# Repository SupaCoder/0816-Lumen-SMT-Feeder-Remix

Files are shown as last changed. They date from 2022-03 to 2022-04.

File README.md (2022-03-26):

# 0816 Lumen SMT Feeder Remix
 0816 SMT Automatic Feeder modified to work with the LumenPNP. Custom firmware written for an arduino nano with a servo sheild can run 12 feeders.

## Notes on printing and assembly
All the files need to be oriented to print correctly on your own printer.
use 0.2mm layer height for ALL parts

There is minimal post processing needed where bridging would help print things in thin air
no supports needed.

Assembly guide coming later when i have time.

Some things that i used
M3 screws for the big holes
M2.5 for the switch and servo armature and the tensioner on the lip
3D printer spring for the tape push down lever
elastic band for the spooler lever
M4 sized hole for mounting to the extrusion

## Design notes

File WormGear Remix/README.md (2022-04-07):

# WormGear Tape puller remix
 0816 SMT Automatic Feeder tape puller modified to better fit onto the feeder. Removed as many screws/pins as I could. 
## Notes on printing and assembly
All the files need to be oriented to print correctly on your own printer.
use 0.2mm layer height for ALL parts
Use Supports for the lever

use 0.1mm layer height for the failure gear with No supports. The outer shell is made to break away "easily" some cleanup required.

for installing the puller on the feeder put the top most screw in first then slide the tape puller onto that screw and put in the bottom one. after tightening both install the bottom motor last.

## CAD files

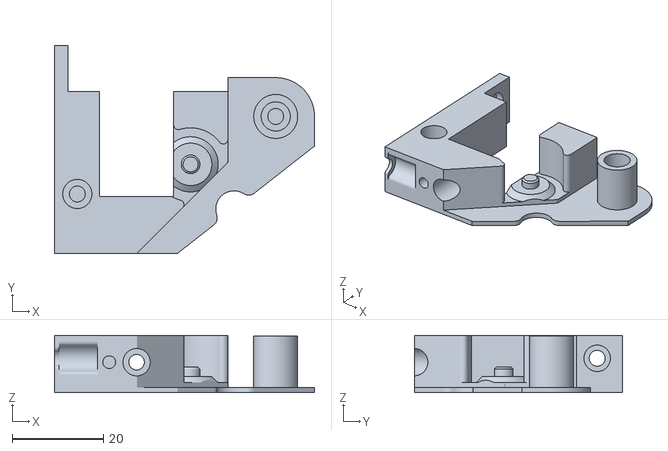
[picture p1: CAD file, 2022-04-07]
WormGear Remix/BodyMain.stl
57.0 x 45.5 x 12.6

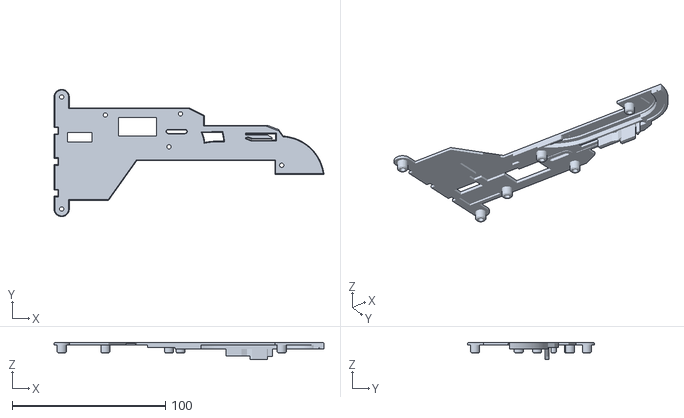
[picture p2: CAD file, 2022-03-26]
3D print files/base_cover.stl
176.1 x 83.0 x 11.2

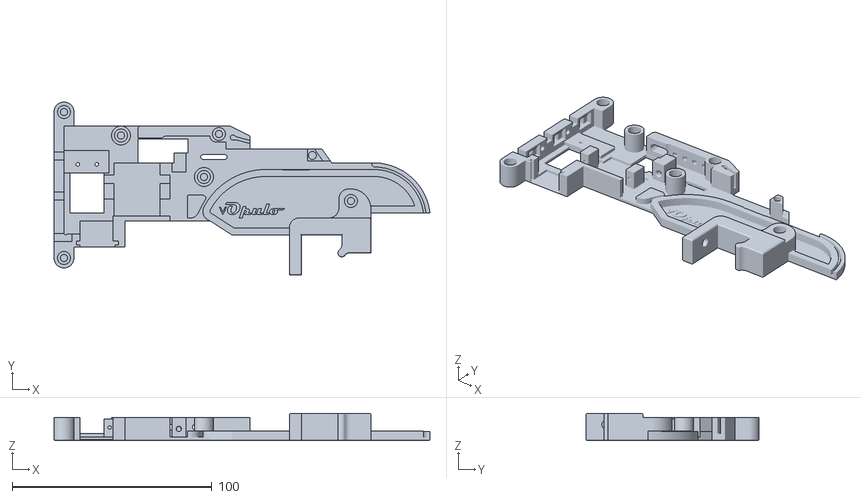
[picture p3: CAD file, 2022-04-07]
Longer Body Feeder/base.stl
188.1 x 86.5 x 13.7

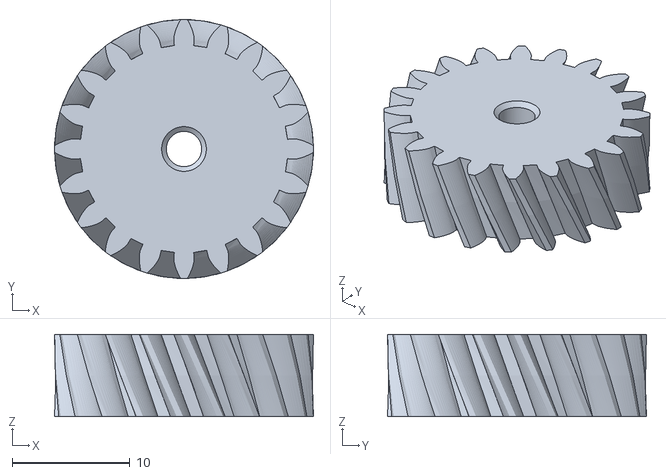
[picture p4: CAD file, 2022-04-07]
WormGear Remix/BigGear.stl
22.0 x 22.0 x 7.00

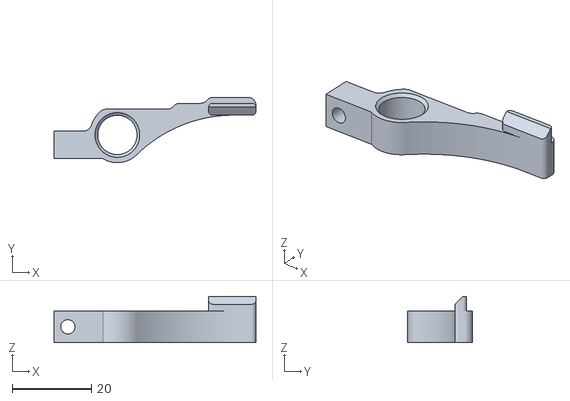
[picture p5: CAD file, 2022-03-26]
3D print files/tape_pushdown_springloaded.stl
51.0 x 16.5 x 11.7

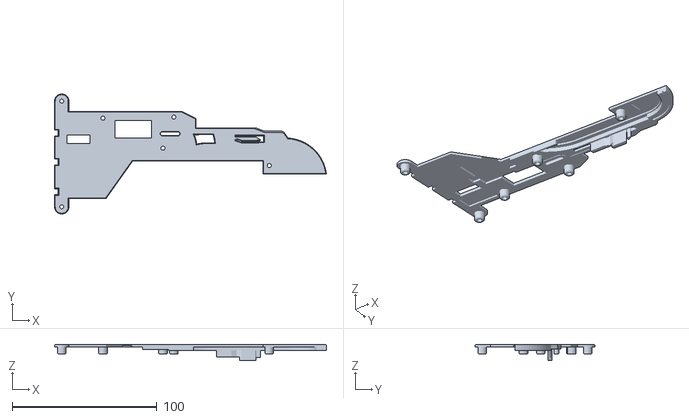
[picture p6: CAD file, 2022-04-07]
Longer Body Feeder/base_cover.stl
188.1 x 83.0 x 11.2

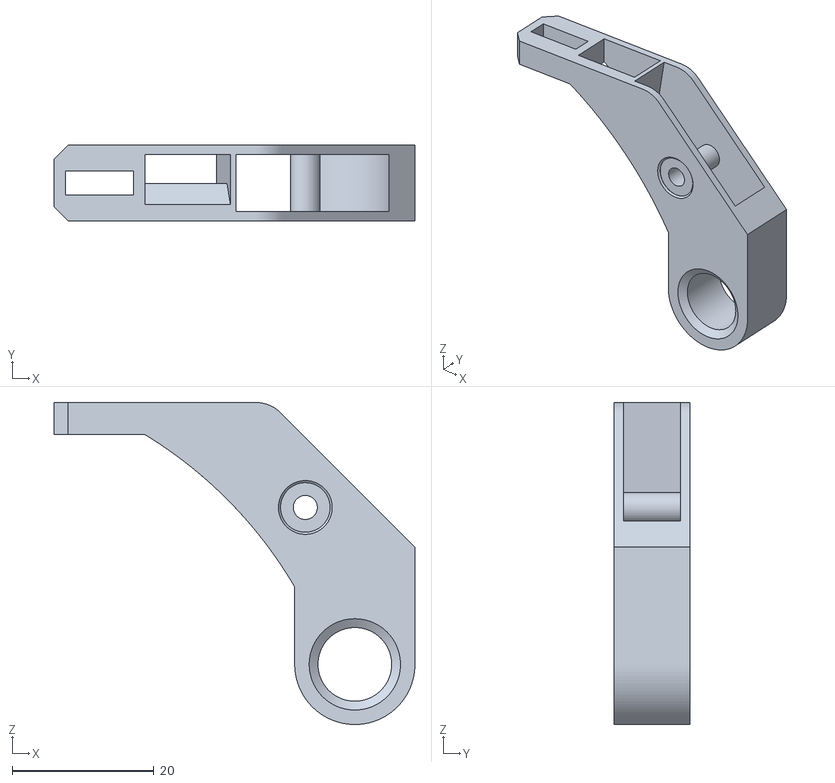
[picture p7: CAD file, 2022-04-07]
WormGear Remix/Lever.stl
51.0 x 10.8 x 45.5

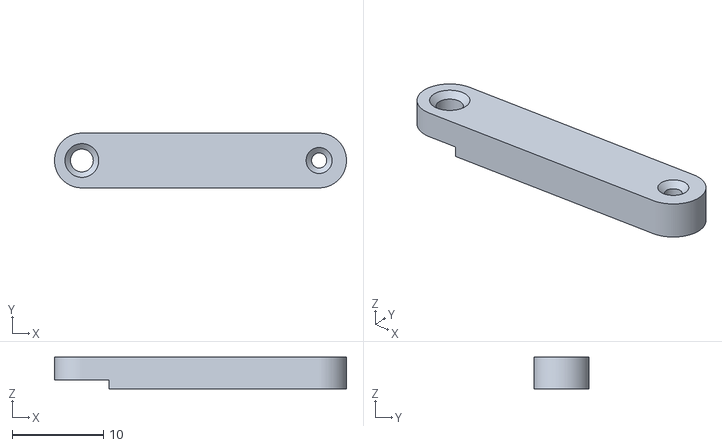
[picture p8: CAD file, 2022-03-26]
3D print files/lever_servo_advancer.stl
32.0 x 6.00 x 3.50

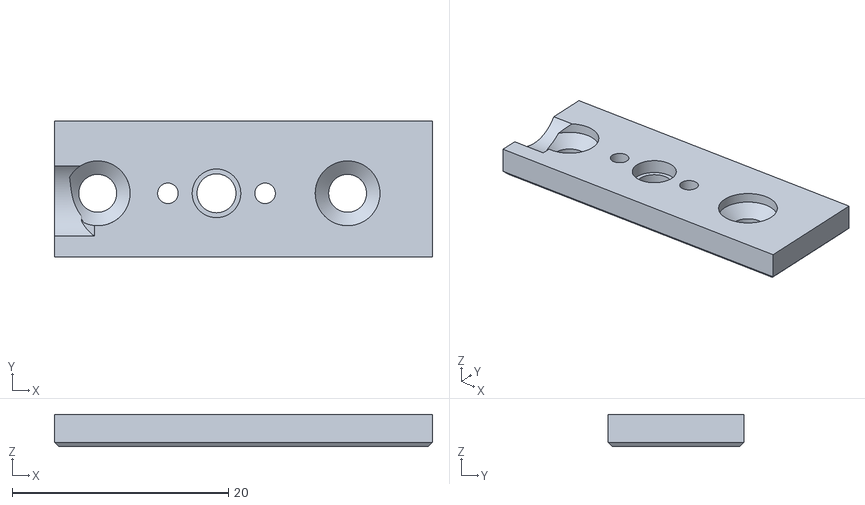
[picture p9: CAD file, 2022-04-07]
WormGear Remix/BodyMount.stl
35.0 x 12.6 x 3.00

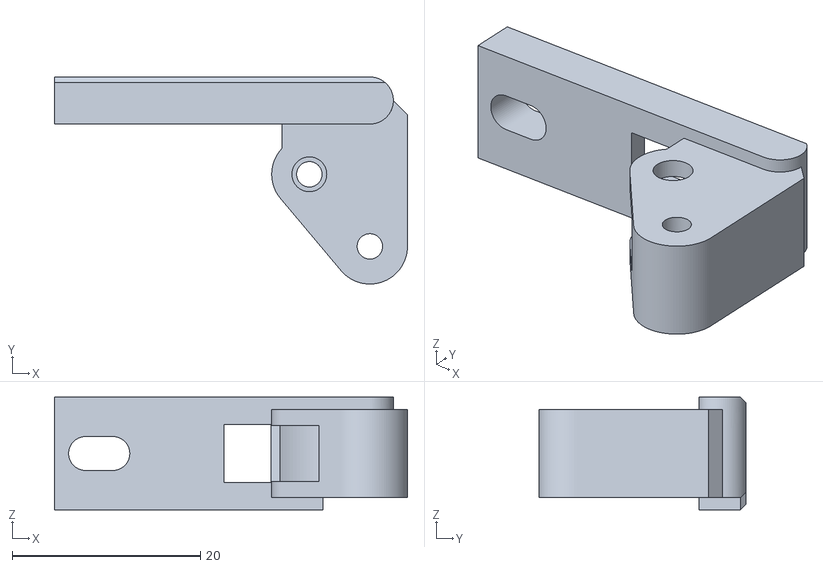
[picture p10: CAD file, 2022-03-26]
3D print files/vorspanner_rad.stl
37.5 x 22.0 x 12.0

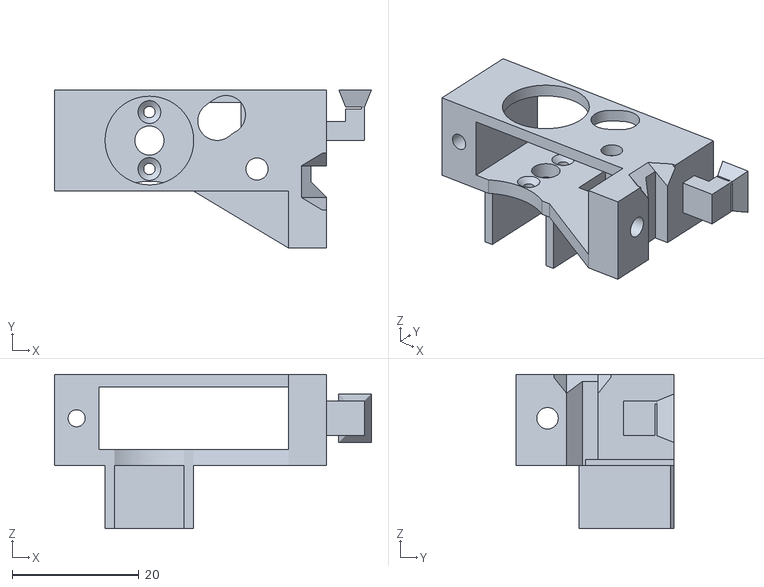
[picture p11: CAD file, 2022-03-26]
3D print files/spooler_mountplate_v2.stl
50.1 x 25.0 x 24.4

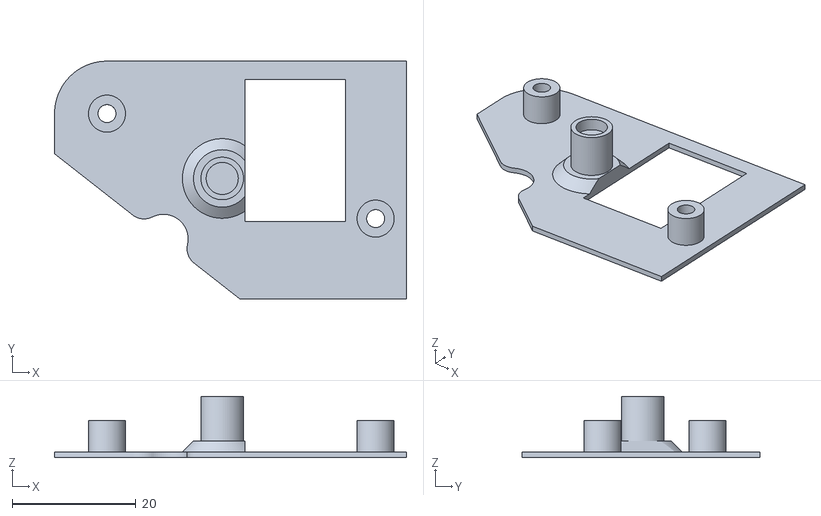
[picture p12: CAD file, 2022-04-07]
WormGear Remix/BodyCover.stl
57.0 x 38.5 x 9.90

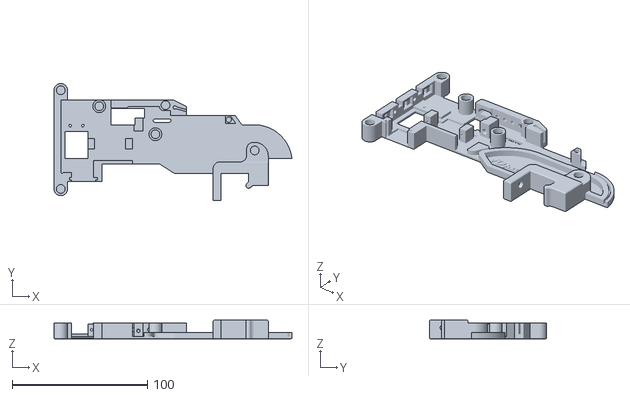
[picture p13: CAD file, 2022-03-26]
3D print files/base.stl
176.1 x 86.5 x 13.7

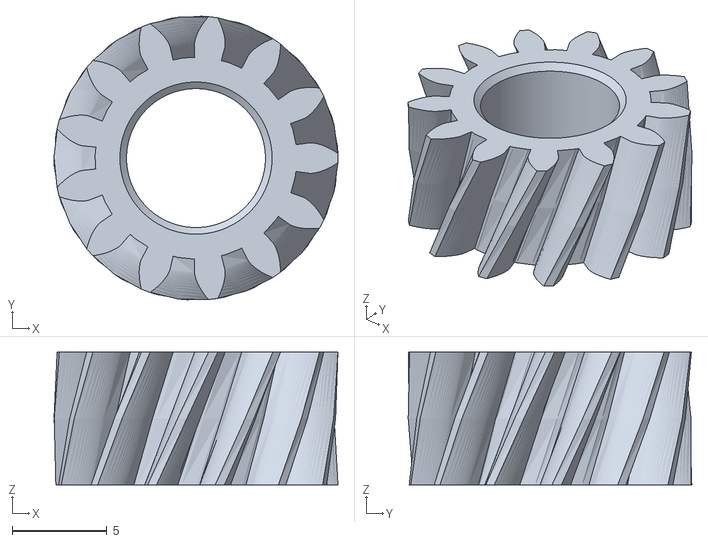
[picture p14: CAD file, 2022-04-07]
WormGear Remix/SmolGear.stl
15.0 x 15.0 x 7.00

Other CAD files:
3D print files/lever_coverswitch_pullingSpring.stl
3D print files/petg_spring_advancer.stl
3D print files/feeder_pin_new.stl
3D print files/DIN - Spur gear 0.7M 17T 20PA Spur gear.stl
3D print files/DIN - Spur gear.stl

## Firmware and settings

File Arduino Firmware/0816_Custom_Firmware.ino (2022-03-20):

#include <Servo.h>

Servo feeder0;
Servo feeder1;
Servo feeder2;
Servo feeder3;
Servo feeder4;
Servo feeder5;
Servo feeder6;
Servo feeder7;
Servo feeder8;
Servo feeder9;
Servo feeder10;
Servo feeder11;

String inData;
void setup() {

  Serial.begin(115200);
  Serial.println("Feeduino");
  Serial.println("ok");

  feeder0.attach(2);
  feeder1.attach(3);
  feeder2.attach(4);
  feeder3.attach(5);
  feeder4.attach(6);
  feeder5.attach(7);
  feeder6.attach(8);
  feeder7.attach(9);
  feeder8.attach(10);
  feeder9.attach(11);
  feeder10.attach(12);
  feeder11.attach(13);
  
//setFeeder(0, 129);
//setFeeder(0, 90);
}

//Fx a
//F - Feeder
//x - number
//a - value

//Fx S
//Feeder 1 Serve

//Set Fx R<> P<>
//Set Feeder x Retract and Push

void loop() {
  while (Serial.available() > 0) {
    char recieved = Serial.read();
    inData += recieved;

    if (recieved == '\n') {
      processCommand(inData);
      inData = "";
    }
  }
}

void processCommand(String inData) {
  inData.trim();
  inData.toUpperCase();
  Serial.print("ok");
  if(inData.startsWith("F")){
    String temp = inData.substring(1);
    servePart(temp.toInt());
    Serial.print(": Served F");
    Serial.print(temp.toInt());
    
  }
  
  Serial.println("");
}

void servePart(int feeder) {
  setFeeder(feeder, 80);//88
  delay(200);
  setFeeder(feeder, 140);
  delay(200);
  setFeeder(feeder, 129);
}

void setFeeder(int feeder, int value) {
  switch (feeder) {
    case 0:
      feeder0.write(value);
      break;
    case 1:
      feeder1.write(value);
      break;
    case 2:
      feeder2.write(value);
      break;
    case 3:
      feeder3.write(value);
      break;
    case 4:
      feeder4.write(value);
      break;
    case 5:
      feeder5.write(value);
      break;
    case 6:
      feeder6.write(value);
      break;
    case 7:
      feeder7.write(value);
      break;
    case 8:
      feeder8.write(value);
      break;
    case 9:
      feeder9.write(value);
      break;
    case 10:
      feeder10.write(value);
      break;
    case 11:
      feeder11.write(value);
      break;
    default:
      break;
  }
}

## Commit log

2022-03-20 Initial commit
    Early working version of the feeder. consider this a Beta, as it will be modified as time goes on and tuned to be a better design
    [DIN - Spur gear 0.7M 17T 20PA Spur gear.stl, DIN - Spur gear.stl, PCB Bracket v1.stl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]
2022-03-26 Many Tweeks to the 3D files.
    Fixed issue with servo missfitment
    Added port for switch pins
    Lever now has external feature to aid in loading and unloading tape
    clearence on the exit improved for larger components
    added a tensioner for the cover that prevents the components from flying out
    Extended stroke of the advancer to aid in clearence of part in the pickup zone
    Added a catch to prevent the tape from jumping off the lever, needs one cut after printing to open the gap
    Beefed up the mounting area to aid in alligning multiple feeders die by side.
    [PCB Bracket v1.stl, base.stl, base_cover.stl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]
2022-04-07 Remixed Worm Gear tape puller + elongated the feeder body
    [BigGear.stl, BodyCover.stl, BodyMain.stl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]
